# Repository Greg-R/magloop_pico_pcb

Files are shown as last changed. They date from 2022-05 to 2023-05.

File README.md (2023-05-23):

#  Printed Circuit Board for Magnetic Loop Antenna Controller

**Please note this repository is no longer active.**

The new repository is here:

(https://github.com/Greg-R/magloop_pico_pcb_2)

Design and fabrication files the Magnetic Loop Antenna Controller printed circuit board.

#  License

Please refer to the LICENSE file included in this repository.

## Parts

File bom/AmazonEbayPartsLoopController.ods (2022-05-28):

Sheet: Amazon
Amazon
Part | URL | Quantity for Project
Stepper Driver Module | https://www.amazon.com/gp/product/B01FFGAKK8
ILI9341 Display Module | https://www.amazon.com/gp/product/B073R7BH1B | 1
AD9850 DDS Module | https://www.amazon.com/gp/product/B01J7XPWNU | 1
Coaxial connector for relay | https://www.amazon.com/gp/product/B08Y7YWF3S | 1
Panel mount fuse holder and fuses | https://www.amazon.com/gp/product/B07VT4VRW7 | 1
Rotary encoders (not modules) with knobs | https://www.amazon.com/gp/product/B07DM2YMT4 | 3
Pushbuttons | https://www.amazon.com/gp/product/B0752RMB7Q | 3
Toggle switch for on/off | https://www.amazon.com/gp/product/B0799NSBHY | 1
Heatsink cooler fin for LM7805 | https://www.amazon.com/gp/product/B07MHT5KNP | 1
8 pin IDC connector with ribbon cable for display | https://www.amazon.com/gp/product/B07FKLHWT7 | 1
6 pin IDC connector with ribbon cable for push buttons and encoders | https://www.amazon.com/gp/product/B075PLZK9X | 2
JST connectors | https://www.amazon.com/gp/product/B01MCZE2HM | 3
JST crimping tool | https://www.amazon.com/gp/product/B01N4L8QMW | 1
Chanzon 1N5711, recommended diode | https://www.amazon.com/gp/product/B079KJBVZV | 4
Ethernet to screw terminal board, used at antenna | https://www.amazon.com/gp/product/B06XZ3BMTL | 1
Cat7 Ethernet Cable Outdoor rated | https://www.amazon.com/Outdoor-Ethernet-SNANSHI-1000Mbit-Waterproof/dp/B06ZZ1SKD6?th=1 | 1
Nylon hardware kit for assembling enclosure | https://www.amazon.com/HVAZI-Metric-Phillips-Screws-Assortment/dp/B07DVD95YY?th=1
Adhesive feet for controller enclosure | https://www.amazon.com/Bumper-Stopper-Protector-Adhesive-Headboard/dp/B0811DSRQB | 4
25 foot BNC cable | https://www.amazon.com/gp/product/B00K4D19IU?th=1 | 1
Plexiglas 10x10 | https://www.amazon.com/gp/product/B089P1KZ44?th=1 | 1
Large pulley 5mm bore | https://www.amazon.com/gp/product/B09NNBQP9T | 1
Small pulley 5mm bore | https://www.amazon.com/gp/product/B07DMWJJ6X?th=1 | 1
Belt, 6mm width, 260mm length | https://www.amazon.com/gp/product/B07B5Y4MGZ | 1
Limit switches | https://www.amazon.com/gp/product/B08CDF3Q6T | 2
Nylon bolts for antenna M8 30mm supports | https://www.amazon.com/gp/product/B012TAVQJW
Nylon bolts for tuner support brackets M8 40mm | https://www.amazon.com/gp/product/B0936RBF53
Nylon bolts for enclosure | https://www.amazon.com/gp/product/B07DVD95YY
Nylon bolts 6mm used on tuner assembly | https://www.amazon.com/gp/product/B07QWM86GX
DIP switches | https://www.amazon.com/gp/product/B07MH572VS | 1

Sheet: eBay
eBay
Part | URL | Quantity for Project
Substitute for cancelled Digikey BNC | https://www.ebay.com/itm/232652734283

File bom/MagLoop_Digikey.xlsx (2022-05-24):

Country of Origin may be different at time of shipment.
The HTSUS and ECCN information shown is for informational purposes only and is not a representation or warranty as to the accuracy or reliability of these classifications. All information is provided "as is" and is subject to change without notice. Any use made of the information provided is without recourse to Digi-Key and at the user's risk.
Index | Manufacturer Part Number | Manufacturer Name | Description | Availability | Stock Status | Attrition % | Requested Quantity 1 | Pack Quantity 1 | Pack Type 1 | Digi-Key Part Number 1 | Unit Price 1 | Extended Price 1 | Minimum Order Quantity 1 | Customer Reference | Requested Part Number | Lead Weeks | Datasheet | Reference Designator | US Import Tariff | Note | Part Status | RoHS Status | ECCN | HTSUS | Country of Origin | Environmental Information | Original Part numbers | Image
1 | PJ-036AH-SMT-TR | CUI Devices | CONN PWR JACK 2X5.5MM SOLDER | 63,562 | In Stock |  | 1 | 1 | Cut Tape (CT) | CP-036AHPJCT-ND | 1.43000 | $1.43 | 1 |  | CP-036AHPJCT-ND | 14 | https://www.cuidevices.com/product/resource/digikeypdf/pj-036ah-smt-tr.pdf |  | N/A |  | Active | ROHS3 Compliant | EAR99 | 8536.69.4040 | China | https://www.cuidevices.com/product/resource/material-compliance/pj-036ah-smt-tr | CP-036AHPJCT-ND | //media.digikey.com/photos/CUI%20Photos/MFG_PJ-036AH-SMT.jpg
2 | UVR1V100MDD | Nichicon | CAP ALUM 10UF 20% 35V RADIAL | 0 | Normally Stocking |  | 1 | 1 | Bulk | 493-1077-ND | 0.25000 | $0.25 | 1 |  | 493-1077-ND | 64 | https://download.datasheets.com/pdfs/2016/10/6/6/6/44/578/nch_/manual/93896153625063e-uvr.pdf |  | N/A |  | Active | ROHS3 Compliant | EAR99 | 8532.22.0020 | Malaysia |  | 493-1077-ND | //media.digikey.com/photos/Nichicon%20Photos/VR%20SERIES%20YELLOW%20HIGHLIGHT%20990-992.jpg
3 | ERJ-P08J752V | Panasonic Electronic Components | RES SMD 7.5K OHM 5% 2/3W 1206 | 2,311 | In Stock |  | 1 | 1 | Cut Tape (CT) | P7.5KALCT-ND | 0.17000 | $0.17 | 1 |  | P7.5KALCT-ND | 54 | https://industrial.panasonic.com/cdbs/www-data/pdf/RDO0000/AOA0000C331.pdf |  | N/A |  | Active | ROHS3 Compliant | EAR99 | 8533.21.0030 | Japan | https://industrial.panasonic.com/cdbs/www-cgi/auto-publishing.cgi?type=ROSU&region=WW&layer=4&cd=AOA0002 | P7.5KALCT-ND | //media.digikey.com/Renders/Panasonic%20Renders/ERJ-1206%20Pkg.jpg
4 | PPPC081LFBN-RC | Sullins Connector Solutions | CONN HDR 8POS 0.1 GOLD PCB | 92,192 | In Stock |  | 1 | 1 | Tray | S7041-ND | 0.67000 | $0.67 | 1 |  | S7041-ND | 11 | //media.digikey.com/pdf/Data%20Sheets/Sullins%20PDFs/Female_Headers.100_DS.pdf |  | N/A |  | Active | ROHS3 Compliant | EAR99 | 8536.69.4040 | Taiwan | https://www.sullinscorp.com/wp-content/uploads/2019/03/Sullins-RoHS-Compliant-Statement.pdf|https://www.sullinscorp.com/wp-content/uploads/2021/05/Sullins-REACH-211-SVHC-Compliant-Statement.pdf | S7041-ND | //media.digikey.com/photos/Sullins%20Photos/PPPC081LFBN-RC.jpg
5 | PPPC101LFBN-RC | Sullins Connector Solutions | CONN HDR 10POS 0.1 GOLD PCB | 130,868 | In Stock |  | 1 | 1 | Tray | S7043-ND | 0.68000 | $0.68 | 1 |  | S7043-ND | 11 | //media.digikey.com/pdf/Data%20Sheets/Sullins%20PDFs/Female_Headers.100_DS.pdf |  | N/A |  | Active | ROHS3 Compliant | EAR99 | 8536.69.4040 | Taiwan | https://www.sullinscorp.com/wp-content/uploads/2019/03/Sullins-RoHS-Compliant-Statement.pdf|https://www.sullinscorp.com/wp-content/uploads/2021/05/Sullins-REACH-211-SVHC-Compliant-Statement.pdf | S7043-ND | //media.digikey.com/photos/Sullins%20Photos/PPPC101LFBN-RC.jpg
6 | 2-406541-3 | TE Connectivity AMP Connectors | CONN MOD JACK 8P8C R/A SHIELDED | 6,301 | In Stock |  | 1 | 1 | Tray | A118429-ND | 2.57000 | $2.57 | 1 |  | A118429-ND | 27 | https://www.te.com/commerce/DocumentDelivery/DDEController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 |  | May apply on shipments to the U.S. |  | Active | RoHS Compliant | EAR99 | 8536.69.4040 | China |  | A118429-ND | //media.digikey.com/photos/TE%20Connectivity/2-406541-3.JPG
7 | ERJ-8GEYJ750V | Panasonic Electronic Components | RES SMD 75 OHM 5% 1/4W 1206 |  |  |  | 1 | 1 | Cut Tape (CT) | P75ECT-ND | 0.15000 | $0.15 | 1 |  | P75ECT-ND | 54 | https://industrial.panasonic.com/ww/products/pt/general-purpose-chip-resistors/models/ERJ8GEYJ750V |  | N/A |  |  | ROHS3 Compliant | EAR99 | 8533.21.0030 | Japan | https://industrial.panasonic.com/cdbs/www-cgi/auto-publishing.cgi?type=ROSU&region=WW&layer=4&cd=AOA0002 | P75ECT-ND | //media.digikey.com/Renders/Panasonic%20Renders/ERJ-1206%20Pkg.jpg
8 | RC1206FR-0710KL | YAGEO | RES 10K OHM 1% 1/4W 1206 | 2,137,700 | In Stock |  | 1 | 1 | Cut Tape (CT) | 311-10.0KFRCT-ND | 0.10000 | $0.10 | 1 |  | 311-10.0KFRCT-ND | 20 | https://www.yageo.com/upload/media/product/productsearch/datasheet/rchip/PYu-RC_Group_51_RoHS_L_11.pdf |  | May apply on shipments to the U.S. |  | Active | ROHS3 Compliant | EAR99 | 8533.21.0030 | Taiwan | https://www.yageo.com/en/Download/Index/certificates#rchip | 311-10.0KFRCT-ND | //media.digikey.com/Renders/Yageo%20Renders/Yageo-0603.jpg
9 | ERJ-8GEYJ513V | Panasonic Electronic Components | RES SMD 51K OHM 5% 1/4W 1206 |  |  |  | 1 | 1 | Cut Tape (CT) | P51KECT-ND | 0.15000 | $0.15 | 1 |  | P51KECT-ND | 54 | https://industrial.panasonic.com/ww/products/pt/general-purpose-chip-resistors/models/ERJ8GEYJ513V |  | N/A |  |  | ROHS3 Compliant | EAR99 | 8533.21.0030 | Japan | https://industrial.panasonic.com/cdbs/www-cgi/auto-publishing.cgi?type=ROSU&region=WW&layer=4&cd=AOA0002 | P51KECT-ND | //media.digikey.com/Renders/Panasonic%20Renders/ERJ-1206%20Pkg.jpg
10 | RMCF1206FT1K00 | Stackpole Electronics Inc | RES 1K OHM 1% 1/4W 1206 | 820,264 | In Stock |  | 1 | 1 | Cut Tape (CT) | RMCF1206FT1K00CT-ND | 0.10000 | $0.10 | 1 |  | RMCF1206FT1K00CT-ND | 17 | https://www.seielect.com/catalog/sei-rmcf_rmcp.pdf |  | May apply on shipments to the U.S. |  | Active | ROHS3 Compliant | EAR99 | 8533.21.0030 | Taiwan | https://www.seielect.com/catalog/reach.pdf|https://www.seielect.com/catalog/cert-of-compliance.pdf|https://www.seielect.com/catalog/SEI-RoHS_Compliance_Status.pdf | RMCF1206FT1K00CT-ND | //media.digikey.com/Renders/Stackpole%20Renders/1206.jpg
11 | PP3-002AH | CUI Devices | CONN PWR PLUG 2.1X5.5MM SOLDER | 3,286 | In Stock |  | 1 | 1 | Bag | CP3-002AH-ND | 1.64000 | $1.64 | 1 |  | CP3-002AH-ND | 15 | https://www.cuidevices.com/product/resource/digikeypdf/pp3-002ah.pdf |  | N/A |  | Active | ROHS3 Compliant | EAR99 | 8536.69.8000 | Taiwan | https://www.cuidevices.com/product/resource/material-compliance/pp3-002ah | CP3-002AH-ND | //media.digikey.com/Photos/CUI%20Photos/PP3-002AH.JPG
12 | 5-1634513-1 | TE Connectivity AMP Connectors | CONN BNC JACK R/A 50 OHM PCB |  | Obsolete |  | 1 |  |  |  |  |  |  |  | A97569-ND | 4 | https://www.te.com/commerce/DocumentDelivery/DDEController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 |  | N/A |  | Obsolete | RoHS Compliant | EAR99 | 8536.69.4010 | Taiwan | http://www.te.com/commerce/alt/SinglePartSearch.do?PN=5-1634513-1&dest=stmt | A97569-ND | //media.digikey.com/Photos/TE%20Connectivity/5-1634513-1.JPG
13 | S2G | SMC Diode Solutions | DIODE GEN PURP 400V 2A SMB | 21,388 | In Stock |  | 1 | 1 | Cut Tape (CT) | 1655-S2GCT-ND | 0.37000 | $0.37 | 1 |  | 1655-S2GCT-ND | 16 | https://www.smc-diodes.com/propdf/S2A-S2M%20N0562%20REV.A.pdf |  | May apply on shipments to the U.S. |  | Active | ROHS3 Compliant | EAR99 | 8541.10.0080 | China | http://www.smc-diodes.com/uploadfile/Declaration%20Letter%20for%20EU%20REACH-3.pdf|http://www.smc-diodes.com/uploadfile/ROHS%20Declaration%20Letter-3.pdf | 1655-S2GCT-ND | //media.digikey.com/Renders/SMC%20Diode%20Solutions/1655;SMB_DO214AA;;2.jpg
14 | CL31B104KBCNNNC | Samsung Electro-Mechanics | CAP CER 0.1UF 50V X7R 1206 | 1,739,651 | In Stock |  | 1 | 1 | Cut Tape (CT) | 1276-1017-1-ND | 0.12000 | $0.12 | 1 |  | 1276-1017-1-ND | 28 | //media.digikey.com/pdf/Data%20Sheets/Samsung%20PDFs/CL31B104KBCNNNC_Spec.pdf |  | N/A |  | Active | ROHS3 Compliant | EAR99 | 8532.24.0020 | Philippines | https://www.samsungsem.com/global/support/certificate/product-stewardship.do|https://www.samsungsem.com/files/fileDown.do?key=ed1dfdfa-645e-4252-b707-17f9b1502dd1 | 1276-1017-1-ND | //media.digikey.com/Renders/Samsung%20Electro-Mechanics%20America/Ceramic-Capacitor-CL-Series.jpg
15 | LM4040C30FTA | Diodes Incorporated | IC VREF SHUNT 0.5% SOT23 | 0 | Normally Stocking |  | 1 | 1 | Cut Tape (CT) | LM4040C30FTADICT-ND | 0.61000 | $0.61 | 1 |  | LM4040C30FTADICT-ND | 69 | https://www.diodes.com/assets/Datasheets/LM4040.pdf |  | May apply on shipments to the U.S. |  | Active | ROHS3 Compliant | EAR99 | 8542.39.0001 | China | https://www.diodes.com/assets/Quality-Reliability-Docs/Master_CofC.pdf | LM4040C30FTADICT-ND | //media.digikey.com/Renders/Diodes%20Renders/SOT-23-3%20PKG.jpg
16 | MBR0580-TP | Micro Commercial Co | DIODE SCHOTTKY 80V 500MA SOD123 | 108,267 | In Stock |  | 1 | 1 | Cut Tape (CT) | MBR0580-TPMSCT-ND | 0.35000 | $0.35 | 1 |  | MBR0580-TPMSCT-ND | 28 | https://www.mccsemi.com/pdf/Products/MBR0520-MBR0580(SOD123).pdf |  | May apply on shipments to the U.S. |  | Active | ROHS3 Compliant | EAR99 | 8541.10.0070 | China | https://www.mccsemi.com/pdf/pbfree/Certification%20of%20RoHS%20Compliance.pdf|https://www.mccsemi.com/pdf/pbfree/Certification%20of%20Compliance%20of%20CaliforniaProposition65.pdf|https://www.mccsemi.com/pdf/pbfree/Certification%20of%20REACH%20Compliance.pdf | MBR0580-TPMSCT-ND | //media.digikey.com/Renders/Micro%20Commercial%20Renders/SOD-123.jpg
17 | ERJ-8GEYJ472V | Panasonic Electronic Components | RES SMD 4.7K OHM 5% 1/4W 1206 | 144,268 | In Stock |  | 1 | 1 | Cut Tape (CT) | P4.7KECT-ND | 0.15000 | $0.15 | 1 |  | P4.7KECT-ND | 54 | https://industrial.panasonic.com/ww/products/pt/general-purpose-chip-resistors/models/ERJ8GEYJ472V |  | N/A |  |  | ROHS3 Compliant | EAR99 | 8533.21.0030 | Japan | https://industrial.panasonic.com/cdbs/www-cgi/auto-publishing.cgi?type=ROSU&region=WW&layer=4&cd=AOA0002 | P4.7KECT-ND | //media.digikey.com/Renders/Panasonic%20Renders/ERJ-1206%20Pkg.jpg
18 | CC1206KRX7R9BB471 | YAGEO | CAP CER 470PF 50V X7R 1206 | 39,533 | In Stock |  | 1 | 1 | Cut Tape (CT) | 311-1167-1-ND | 0.23000 | $0.23 | 1 |  | 311-1167-1-ND | 20 | https://www.yageo.com/upload/media/product/productsearch/datasheet/mlcc/UPY-GPHC_X7R_6.3V-to-50V_20.pdf |  | N/A |  | Active | ROHS3 Compliant | EAR99 | 8532.24.0020 | Taiwan |  | 311-1167-1-ND | //media.digikey.com/Renders/Yageo%20Renders/1206%280%5E7mm%20thickness%29.jpg
19 | B2B-XH-A-GU | JST Sales America Inc. | CONN HEADER VERT 2POS 2.5MM | 54,025 | In Stock |  | 1 | 1 | Bulk | 455-2946-ND | 0.24000 | $0.24 | 1 |  | 455-2946-ND | 34 | https://www.jst-mfg.com/product/pdf/eng/eXH.pdf |  | N/A |  | Active | RoHS Compliant | EAR99 | 8536.69.4040 | China |  | 455-2946-ND | //media.digikey.com/Photos/JST%20Photos/B2B-XH-A-GU.JPG
20 | DMP31D0U-7 | Diodes Incorporated | MOSFET P-CH 30V 530MA SOT23 | 649 | In Stock |  | 1 | 1 | Cut Tape (CT) | DMP31D0U-7DICT-ND | 0.47000 | $0.47 | 1 |  | DMP31D0U-7DICT-ND | 90 | https://www.diodes.com/assets/Datasheets/DMP31D0U.pdf |  | May apply on shipments to the U.S. |  | Active | ROHS3 Compliant | EAR99 | 8541.21.0095 | China | https://www.diodes.com/assets/Quality-Reliability-Docs/Master_CofC.pdf | DMP31D0U-7DICT-ND | //media.digikey.com/Renders/Diodes%20Renders/SOT-23-3%20PKG.jpg
21 | MMBT3904,215 | Nexperia USA Inc. | TRANS NPN 40V 0.2A TO236AB | 507,080 | In Stock |  | 1 | 1 | Cut Tape (CT) | 1727-4044-1-ND | 0.12000 | $0.12 | 1 |  | 1727-4044-1-ND | 27 | https://assets.nexperia.com/documents/data-sheet/MMBT3904.pdf |  | May apply on shipments to the U.S. |  | Active | ROHS3 Compliant | EAR99 | 8541.21.0075 | China |  | 1727-4044-1-ND | //media.digikey.com/Photos/Nexperia/MFG_SOT23.jpg
22 | LM358P | Texas Instruments | IC OPAMP GP 2 CIRCUIT 8DIP | 13,317 | In Stock |  | 2 | 2 | Tube | 296-1395-5-ND | 0.49000 | $0.98 | 1 |  | 296-1395-5-ND | 35 | https://www.ti.com/general/docs/suppproductinfo.tsp?distId=10 |  | May apply on shipments to the U.S. |  | Active | ROHS3 Compliant | EAR99 | 8542.33.0001 | China |  | 296-1395-5-ND | //media.digikey.com/Photos/Rochester/MFG_TC254P.jpg.jpg
23 | ERJ-8GEYJ272V | Panasonic Electronic Components | RES SMD 2.7K OHM 5% 1/4W 1206 | 149,367 | In Stock |  | 1 | 1 | Cut Tape (CT) | P2.7KECT-ND | 0.15000 | $0.15 | 1 |  | P2.7KECT-ND | 54 | https://industrial.panasonic.com/ww/products/pt/general-purpose-chip-resistors/models/ERJ8GEYJ272V |  | N/A |  |  | ROHS3 Compliant | EAR99 | 8533.21.0030 | Japan | https://industrial.panasonic.com/cdbs/www-cgi/auto-publishing.cgi?type=ROSU&region=WW&layer=4&cd=AOA0002 | P2.7KECT-ND | //media.digikey.com/Renders/Panasonic%20Renders/ERJ-1206%20Pkg.jpg
24 | ERJ-8ENF5100V | Panasonic Electronic Components | RES SMD 510 OHM 1% 1/4W 1206 | 76,423 | In Stock |  | 1 | 1 | Cut Tape (CT) | P510FCT-ND | 0.20000 | $0.20 | 1 |  | P510FCT-ND | 54 | https://industrial.panasonic.com/cdbs/www-data/pdf/RDA0000/AOA0000C304.pdf |  | N/A |  |  | ROHS3 Compliant | EAR99 | 8533.21.0030 | Japan | https://industrial.panasonic.com/cdbs/www-cgi/auto-publishing.cgi?type=ROSU&region=WW&layer=4&cd=AOA0002 | P510FCT-ND | //media.digikey.com/Renders/Panasonic%20Renders/ERJ-1206%20Pkg.jpg
25 | ERJ-P08J201V | Panasonic Electronic Components | RES SMD 200 OHM 5% 2/3W 1206 | 15,554 | In Stock |  | 1 | 1 | Cut Tape (CT) | P200ALCT-ND | 0.17000 | $0.17 | 1 |  | P200ALCT-ND | 54 | https://industrial.panasonic.com/cdbs/www-data/pdf/RDO0000/AOA0000C331.pdf |  | N/A |  | Active | ROHS3 Compliant | EAR99 | 8533.21.0030 | Japan | https://industrial.panasonic.com/cdbs/www-cgi/auto-publishing.cgi?type=ROSU&region=WW&layer=4&cd=AOA0002 | P200ALCT-ND | //media.digikey.com/Renders/Panasonic%20Renders/ERJ-1206%20Pkg.jpg
26 | ERJ-8ENF43R0V | Panasonic Electronic Components | RES SMD 43 OHM 1% 1/4W 1206 | 56,385 | In Stock |  | 1 | 1 | Cut Tape (CT) | P43.0FCT-ND | 0.20000 | $0.20 | 1 |  | P43.0FCT-ND | 54 | https://industrial.panasonic.com/cdbs/www-data/pdf/RDA0000/AOA0000C304.pdf |  | N/A |  |  | ROHS3 Compliant | EAR99 | 8533.21.0030 | Japan | https://industrial.panasonic.com/cdbs/www-cgi/auto-publishing.cgi?type=ROSU&region=WW&layer=4&cd=AOA0002 | P43.0FCT-ND | //media.digikey.com/Renders/Panasonic%20Renders/ERJ-1206%20Pkg.jpg
27 | ERJ-8GEYJ391V | Panasonic Electronic Components | RES SMD 390 OHM 5% 1/4W 1206 | 211,714 | In Stock |  | 1 | 1 | Cut Tape (CT) | P390ECT-ND | 0.15000 | $0.15 | 1 |  | P390ECT-ND | 54 | https://industrial.panasonic.com/ww/products/pt/general-purpose-chip-resistors/models/ERJ8GEYJ391V |  | N/A |  |  | ROHS3 Compliant | EAR99 | 8533.21.0030 | Japan | https://industrial.panasonic.com/cdbs/www-cgi/auto-publishing.cgi?type=ROSU&region=WW&layer=4&cd=AOA0002 | P390ECT-ND | //media.digikey.com/Renders/Panasonic%20Renders/ERJ-1206%20Pkg.jpg
28 | ERJ-8ENF24R9V | Panasonic Electronic Components | RES SMD 24.9 OHM 1% 1/4W 1206 | 5,357 | In Stock |  | 1 | 1 | Cut Tape (CT) | P24.9FCT-ND | 0.20000 | $0.20 | 1 |  | P24.9FCT-ND | 54 | https://industrial.panasonic.com/cdbs/www-data/pdf/RDA0000/AOA0000C304.pdf |  | N/A |  |  | ROHS3 Compliant | EAR99 | 8533.21.0030 | Japan | https://industrial.panasonic.com/cdbs/www-cgi/auto-publishing.cgi?type=ROSU&region=WW&layer=4&cd=AOA0002 | P24.9FCT-ND | //media.digikey.com/Renders/Panasonic%20Renders/ERJ-1206%20Pkg.jpg
29 | ERJ-8GEYJ222V | Panasonic Electronic Components | RES SMD 2.2K OHM 5% 1/4W 1206 | 1,505,502 | In Stock |  | 1 | 1 | Cut Tape (CT) | P2.2KECT-ND | 0.15000 | $0.15 | 1 |  | P2.2KECT-ND | 54 | https://industrial.panasonic.com/ww/products/pt/general-purpose-chip-resistors/models/ERJ8GEYJ222V |  | N/A |  |  | ROHS3 Compliant | EAR99 | 8533.21.0030 | Japan | https://industrial.panasonic.com/cdbs/www-cgi/auto-publishing.cgi?type=ROSU&region=WW&layer=4&cd=AOA0002 | P2.2KECT-ND | //media.digikey.com/Renders/Panasonic%20Renders/ERJ-1206%20Pkg.jpg
30 | ERJ-8GEYJ510V | Panasonic Electronic Components | RES SMD 51 OHM 5% 1/4W 1206 | 43,802 | In Stock |  | 1 | 1 | Cut Tape (CT) | P51ECT-ND | 0.15000 | $0.15 | 1 |  | P51ECT-ND | 54 | https://industrial.panasonic.com/ww/products/pt/general-purpose-chip-resistors/models/ERJ8GEYJ510V |  | N/A |  |  | ROHS3 Compliant | EAR99 | 8533.21.0030 | Japan | https://industrial.panasonic.com/cdbs/www-cgi/auto-publishing.cgi?type=ROSU&region=WW&layer=4&cd=AOA0002 | P51ECT-ND | //media.digikey.com/Renders/Panasonic%20Renders/ERJ-1206%20Pkg.jpg
31 | ERJ-8GEYJ105V | Panasonic Electronic Components | RES SMD 1M OHM 5% 1/4W 1206 | 116,279 | In Stock |  | 1 | 1 | Cut Tape (CT) | P1.0MECT-ND | 0.15000 | $0.15 | 1 |  | P1.0MECT-ND | 54 | https://industrial.panasonic.com/ww/products/pt/general-purpose-chip-resistors/models/ERJ8GEYJ105V |  | N/A |  |  | ROHS3 Compliant | EAR99 | 8533.21.0030 | Japan | https://industrial.panasonic.com/cdbs/www-cgi/auto-publishing.cgi?type=ROSU&region=WW&layer=4&cd=AOA0002 | P1.0MECT-ND | //media.digikey.com/Renders/Panasonic%20Renders/ERJ-1206%20Pkg.jpg
32 | ERJ-8GEYJ243V | Panasonic Electronic Components | RES SMD 24K OHM 5% 1/4W 1206 | 20,248 | In Stock |  | 1 | 1 | Cut Tape (CT) | P24KECT-ND | 0.15000 | $0.15 | 1 |  | P24KECT-ND | 54 | https://industrial.panasonic.com/ww/products/pt/general-purpose-chip-resistors/models/ERJ8GEYJ243V |  | N/A |  |  | ROHS3 Compliant | EAR99 | 8533.21.0030 | Japan | https://industrial.panasonic.com/cdbs/www-cgi/auto-publishing.cgi?type=ROSU&region=WW&layer=4&cd=AOA0002 | P24KECT-ND | //media.digikey.com/Renders/Panasonic%20Renders/ERJ-1206%20Pkg.jpg
33 | PPPC201LFBN-RC | Sullins Connector Solutions | CONN HDR 20POS 0.1 GOLD PCB | 14,630 | In Stock |  | 1 | 1 | Tray | S7053-ND | 1.28000 | $1.28 | 1 |  | S7053-ND | 11 | //media.digikey.com/pdf/Data%20Sheets/Sullins%20PDFs/Female_Headers.100_DS.pdf |  | N/A |  | Active | ROHS3 Compliant | EAR99 | 8536.69.4040 | Taiwan | https://www.sullinscorp.com/wp-content/uploads/2019/03/Sullins-RoHS-Compliant-Statement.pdf|https://www.sullinscorp.com/wp-content/uploads/2021/05/Sullins-REACH-211-SVHC-Compliant-Statement.pdf | S7053-ND | //media.digikey.com/photos/Sullins%20Photos/PPPC201LFBN-RC.jpg
34 | PH1-20-UA | Adam Tech | CONN HEADER VERT 20POS 2.54MM | 11,761 | In Stock |  | 1 | 1 | Bag | 2057-PH1-20-UA-ND | 0.32000 | $0.32 | 1 |  | 2057-PH1-20-UA-ND | 10 | https://app.adam-tech.com/products/download/data_sheet/201605/ph1-xx-ua-data-sheet.pdf |  | N/A |  | Active | ROHS3 Compliant | EAR99 | 8536.69.4040 | Taiwan |  | 2057-PH1-20-UA-ND | //media.digikey.com/Renders/Adam-Tech%20Renders/PH1-xx-UA.jpg

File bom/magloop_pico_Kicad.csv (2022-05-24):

Source: | /home/raven/gitrepos/pcb/magloop_pico_pcb/magloop_pico.kicad_sch
Date: | Tue 24 May 2022 03:14:49 PM EDT
Tool: | Eeschema 6.0.5-a6ca702e91~116~ubuntu20.04.1
Generator: | /usr/share/kicad/plugins/bom_csv_grouped_by_value_with_fp.py
Component Count: | 102
Ref | Qnty | Value | Cmp name | Footprint | Description | Vendor
C1, C6, C7, C19, | 4 | 10 uF | C_Polarized_US | Capacitor_THT:CP_Radial_D5.0mm_P2.00mm | Polarized capacitor, US symbol
C2, C3, C4, C5, C8, C9, C10, C13, C14, C15, C16, C17, C18, C20, C23, C24, C25, C28, C29, | 19 | 0.1uF | C | Capacitor_SMD:C_1206_3216Metric_Pad1.33x1.80mm_HandSolder | Unpolarized capacitor
C11, C12, C21, C22, C26, C27, | 6 | 470pF | C | Capacitor_SMD:C_1206_3216Metric_Pad1.33x1.80mm_HandSolder | Unpolarized capacitor
D1, | 1 | MBR0520LT1G | MBR0520LT1G | digikey-footprints:SOD-123 | DIODE SCHOTTKY 20V 500MA SOD123
D2, D3, D4, D5, | 4 | 1N5711 | 1N5711UR | Diode_THT:D_DO-35_SOD27_P7.62mm_Horizontal | 70V 33mA Schottky diode, MELF(DO-213AA)
D6, | 1 | 1N4004 | 1N4004 | Diode_SMD:D_SMB | 400V 1A General Purpose Rectifier Diode, DO-41
FB1, | 1 | FerriteBead | FerriteBead | Inductor_SMD:L_1206_3216Metric | Ferrite bead
J1, | 1 | Conn_Coaxial_Power | Conn_Coaxial_Power | Connector_BarrelJack:BarrelJack_CUI_PJ-036AH-SMT_Horizontal | coaxial connector (BNC, SMA, SMB, SMC, Cinch/RCA, LEMO, ...)
J2, J4, | 2 | Conn_02x03_Odd_Even | Conn_02x03_Odd_Even | Connector_IDC:IDC-Header_2x03_P2.54mm_Vertical | Generic connector, double row, 02x03, odd/even pin numbering scheme (row 1 odd numbers, row 2 even numbers), script generated (kicad-library-utils/schlib/autogen/connector/)
J3, | 1 | POWER SW | B2B-XH-A_LF__SN_ | digikey-footprints:PinHeader_1x2_P2.5mm_Drill1.1mm | CONN HEADER VERT 2POS 2.5MM
J5, | 1 | Conn_02x04_Odd_Even | Conn_02x04_Odd_Even | Connector_IDC:IDC-Header_2x04_P2.54mm_Vertical | Generic connector, double row, 02x04, odd/even pin numbering scheme (row 1 odd numbers, row 2 even numbers), script generated (kicad-library-utils/schlib/autogen/connector/)
J6, | 1 | TO RF RELAY | B2B-XH-A_LF__SN_ | digikey-footprints:PinHeader_1x2_P2.5mm_Drill1.1mm | CONN HEADER VERT 2POS 2.5MM
J7, | 1 | ETHERNET | 2-406541-3 | magloop_library:2-406541-3
J8, | 1 | 5-1634513-1 | 5-1634513-1 | 5-1634513-1:TE_5-1634513-1
J9, | 1 | 12V AUDIO MUTE | B2B-XH-A_LF__SN_ | digikey-footprints:PinHeader_1x2_P2.5mm_Drill1.1mm | CONN HEADER VERT 2POS 2.5MM
J10, | 1 | 5V AUDIO MUTE | B2B-XH-A_LF__SN_ | digikey-footprints:PinHeader_1x2_P2.5mm_Drill1.1mm | CONN HEADER VERT 2POS 2.5MM
Q1, Q2, Q3, Q4, Q5, Q6, Q7, Q9, Q11, | 9 | NPN | MMBT3904 | Package_TO_SOT_SMD:SOT-23_Handsoldering | 0.2A Ic, 40V Vce, Small Signal NPN Transistor, SOT-23
Q8, Q10, Q12, | 3 | PMOS | Si2371EDS | Package_TO_SOT_SMD:SOT-23_Handsoldering | -3.6A Id, -30V Vds, P-Channel MOSFET, SOT-23
R1, | 1 | 7.5K | R_US | Resistor_SMD:R_1206_3216Metric_Pad1.30x1.75mm_HandSolder | Resistor, US symbol
R2, | 1 | 2.7K | R_US | Resistor_SMD:R_1206_3216Metric_Pad1.30x1.75mm_HandSolder | Resistor, US symbol
R3, | 1 | 510 | R_US | Resistor_SMD:R_1206_3216Metric_Pad1.30x1.75mm_HandSolder | Resistor, US symbol
R4, | 1 | 200 | R_US | Resistor_SMD:R_1206_3216Metric_Pad1.30x1.75mm_HandSolder | Resistor, US symbol
R5, | 1 | 43 | R_US | Resistor_SMD:R_1206_3216Metric_Pad1.30x1.75mm_HandSolder | Resistor, US symbol
R6, | 1 | 75 | R_US | Resistor_SMD:R_1206_3216Metric_Pad1.30x1.75mm_HandSolder | Resistor, US symbol
R7, | 1 | 390 | R_US | Resistor_SMD:R_1206_3216Metric_Pad1.30x1.75mm_HandSolder | Resistor, US symbol
R8, | 1 | 2.2K | R_US | Resistor_SMD:R_1206_3216Metric_Pad1.30x1.75mm_HandSolder | Resistor, US symbol
R10, | 1 | 24.9 | R_US | Resistor_SMD:R_1206_3216Metric_Pad1.30x1.75mm_HandSolder | Resistor, US symbol
R13, R14, R15, R16, | 4 | 51.0 | R_US | Resistor_SMD:R_1206_3216Metric_Pad1.30x1.75mm_HandSolder | Resistor, US symbol
R17, R18, | 2 | 4.7K | R_US | Resistor_SMD:R_1206_3216Metric_Pad1.30x1.75mm_HandSolder | Resistor, US symbol
R20, R21, | 2 | 1M | R_US | Resistor_SMD:R_1206_3216Metric_Pad1.30x1.75mm_HandSolder | Resistor, US symbol
R22, R23, | 2 | 51K | R_US | Resistor_SMD:R_1206_3216Metric_Pad1.30x1.75mm_HandSolder | Resistor, US symbol
R24, R25, | 2 | 1K | R_US | Resistor_SMD:R_1206_3216Metric_Pad1.30x1.75mm_HandSolder | Resistor, US symbol
R26, R27, R30, R31, R32, R33, R34, R35, R36, R37, R38, R39, R40, | 13 | 10K | R_US | Resistor_SMD:R_1206_3216Metric_Pad1.30x1.75mm_HandSolder | Resistor, US symbol
R28, R29, | 2 | 24K | R_US | Resistor_SMD:R_1206_3216Metric_Pad1.30x1.75mm_HandSolder | Resistor, US symbol
SW1, | 1 | SW_DIP_x03 | SW_DIP_x03 | digikey-footprints:DIP-6_W7.62mm | 3x DIP Switch, Single Pole Single Throw (SPST) switch, small symbol
U1, | 1 | AD9850MODULE | AD9850MODULE | magloop_pico:AD9850_MODULE
U2, | 1 | A4988_Module | A4988_Module | magloop_pico:A4988_MODULE
U3, | 1 | LM7805 | LM7805_TO220 | Package_TO_SOT_THT:TO-220-3_Vertical | Positive 1A 35V Linear Regulator, Fixed Output 5V, TO-220
U4, | 1 | PI_PICO | PI_PICO | magloop_pico:PI_PICO
U5, | 1 | LM4040DBZ-3 | LM4040DBZ-3 | Package_TO_SOT_SMD:SOT-23_Handsoldering | 3.000V Precision Micropower Shunt Voltage Reference, SOT-23
U7, U8, | 2 | LM358 | LM358 | Package_DIP:DIP-8_W7.62mm | Low-Power, Dual Operational Amplifiers, DIP-8/SOIC-8/TO-99-8

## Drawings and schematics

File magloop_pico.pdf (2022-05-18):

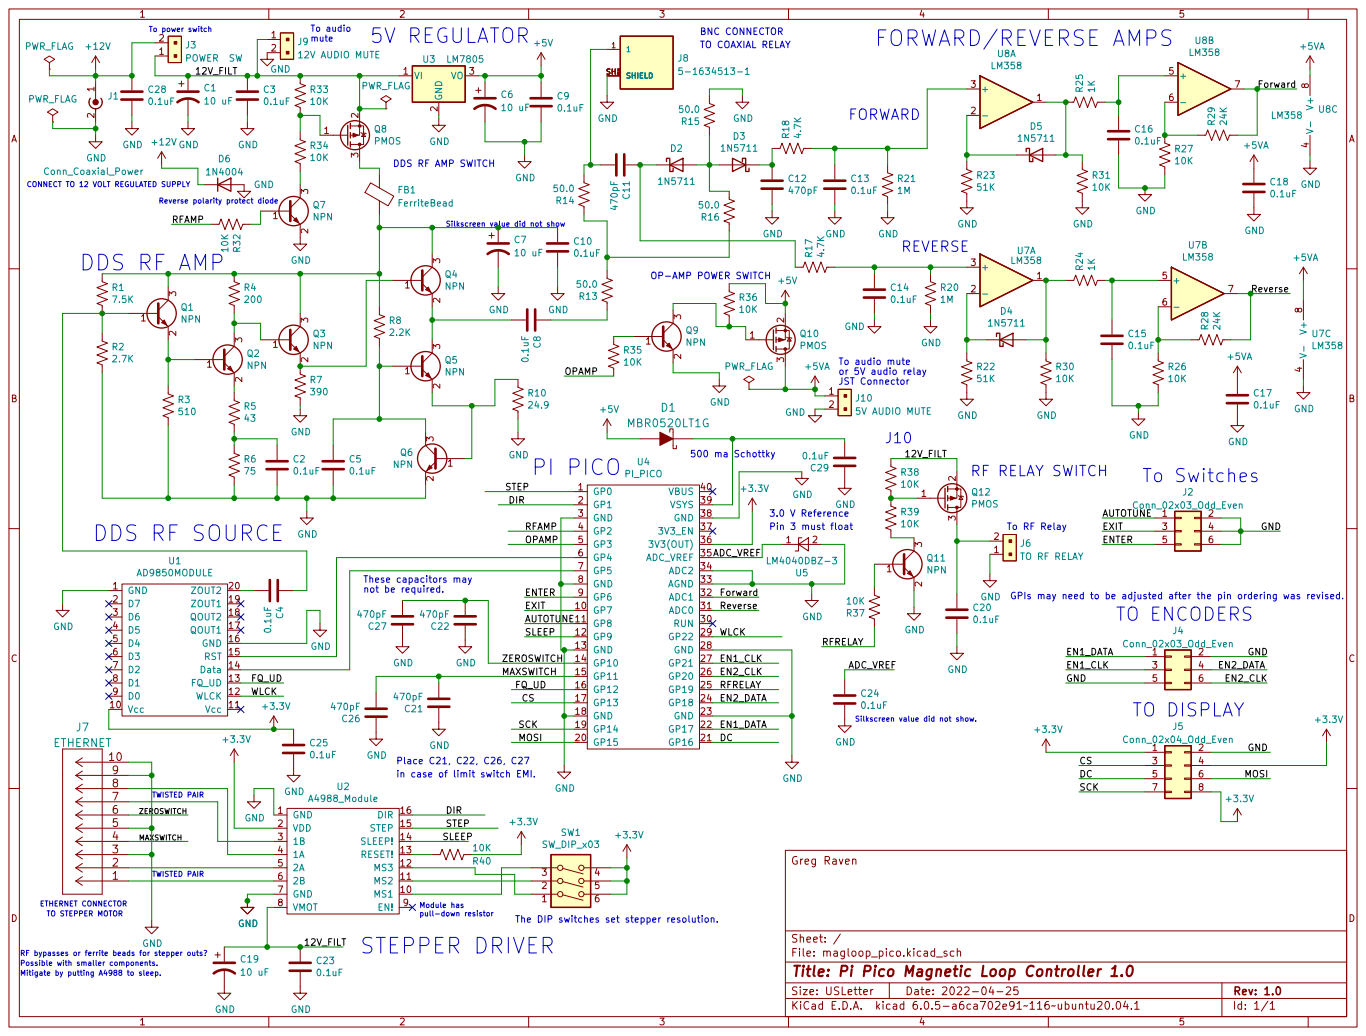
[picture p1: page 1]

To power switch CONNECT TO 12 VOLT REGULATED SUPPLY
PWR_FLAG

GPIs may need to be adjusted after the pin ordering was revised. DDS RF AMP SWITCH

Silkscreen value did not show

2 3 Q12 PMOS GND GND GND

3.0 V Reference Pin 3 must float DDS RF AMP

OP-AMP POWER SWITCH

not be required. TO STEPPER MOTOR

Silkscreen value did not show. TWISTED PAIR

7 | TWISTED PAIR

File: magloop_pico.kicad_sch Sheet: / Greg Raven

The DIP switches set stepper resolution.

RF bypasses or ferrite beads for stepper outs? Possible with smaller components.

Id: 1/1 Title: Pi Pico Magnetic Loop Controller 1.0

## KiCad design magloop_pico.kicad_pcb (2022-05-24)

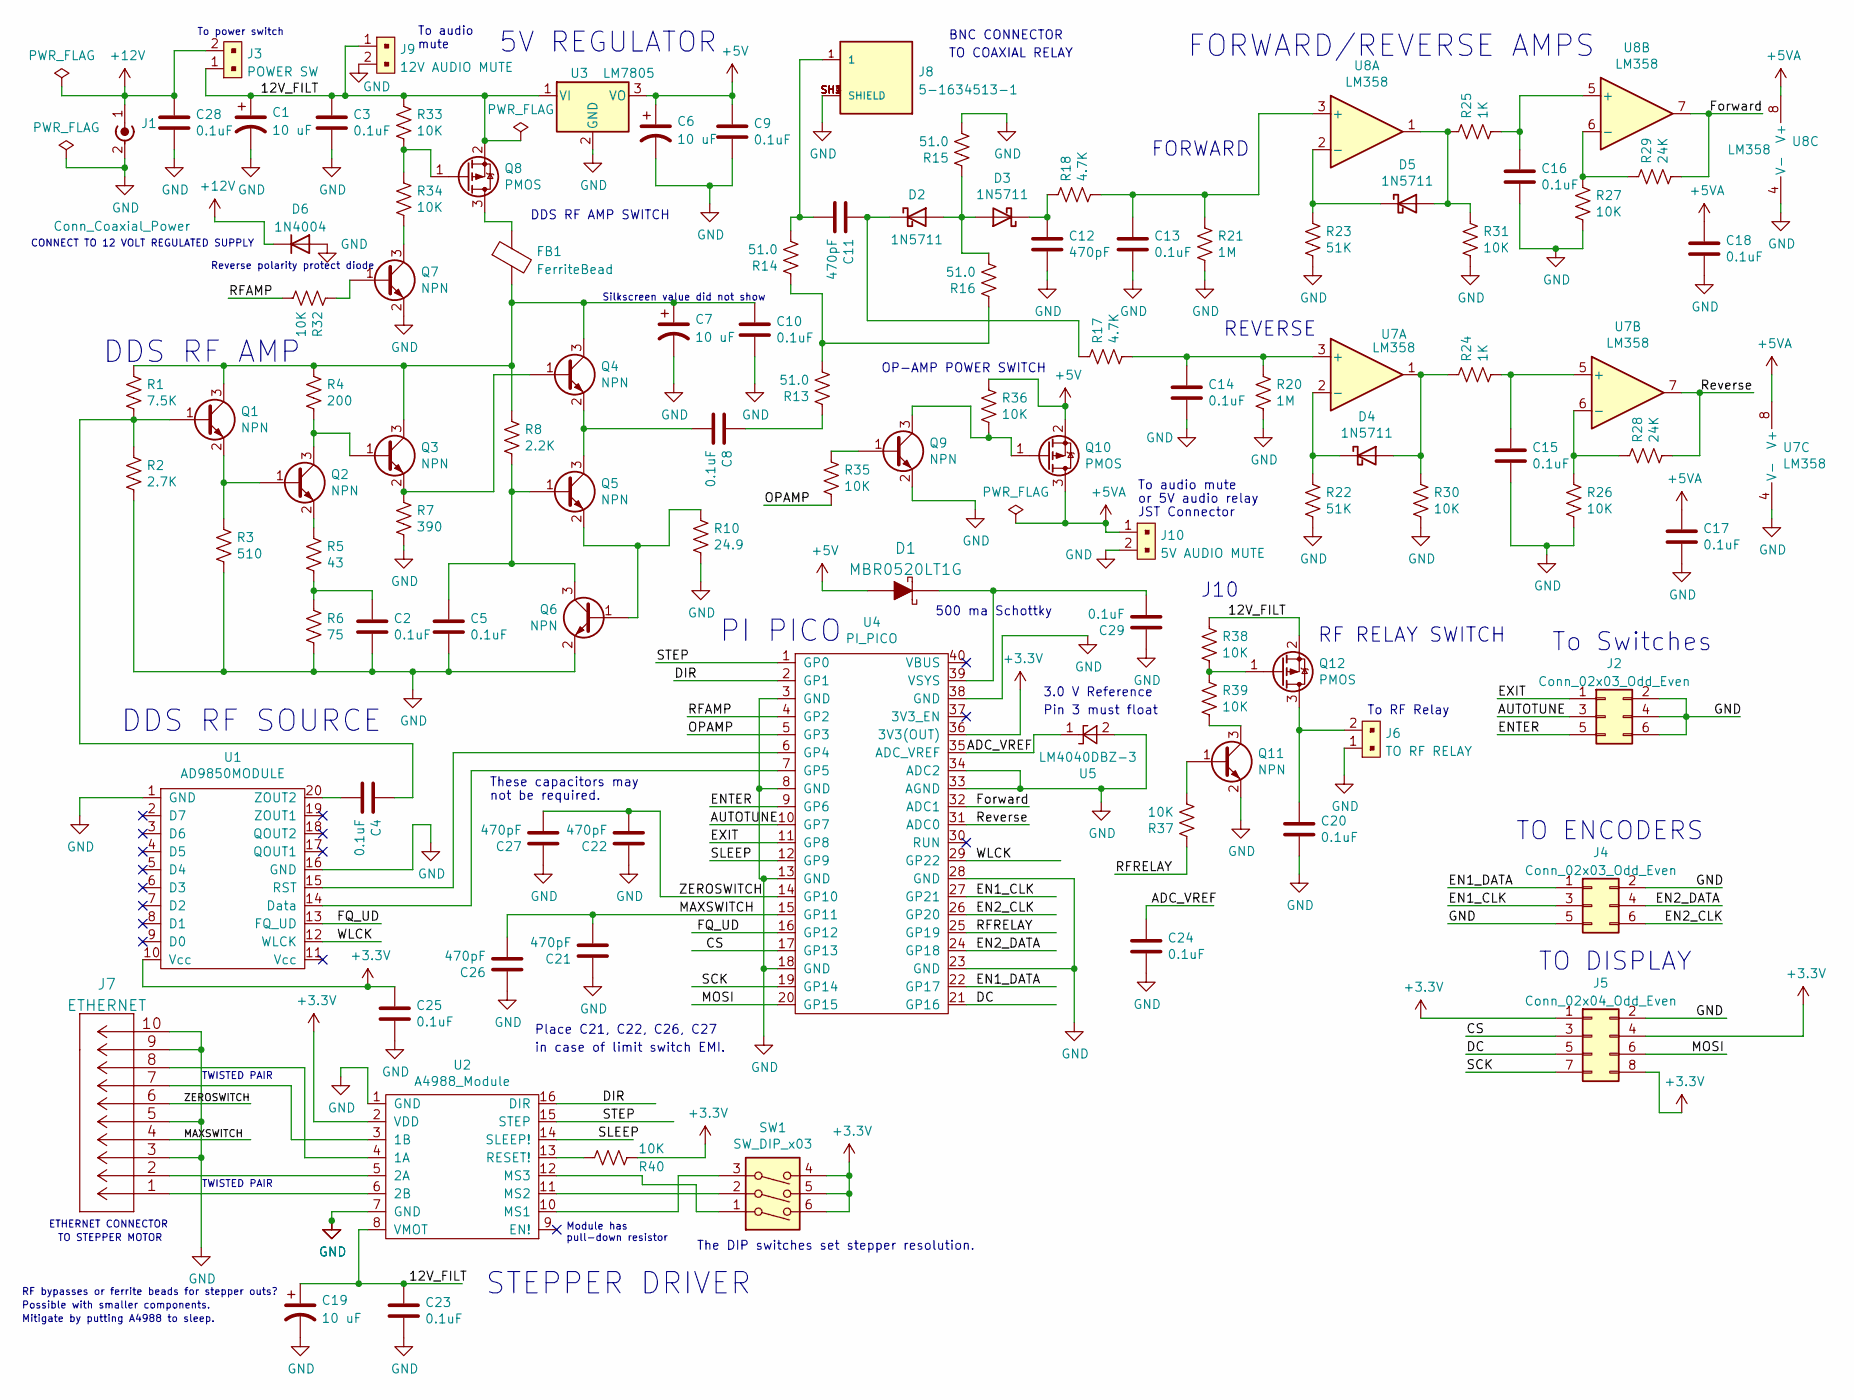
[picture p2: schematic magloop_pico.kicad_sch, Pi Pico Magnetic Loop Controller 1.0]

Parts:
C1, C6, C7, C19: 10 uF; CP_Radial_D5.0mm_P2.00mm
C2, C3, C4, C5, C8, C9, C10, C13, C14, C15, C16, C17, C18, C20, C23, C24, C25, C28, C29: 0.1uF; C_1206_3216Metric_Pad1.33x1.80mm_HandSolder
C11, C12, C21, C22, C26, C27: 470pF; C_1206_3216Metric_Pad1.33x1.80mm_HandSolder
D1: MBR0520LT1G; SOD-123; MPN MBR0520LT1G; Digi-Key_PN MBR0520LT1GOSCT-ND
D2, D3, D4, D5: 1N5711; D_DO-35_SOD27_P7.62mm_Horizontal
D6: 1N4004; D_SMB
FB1: FerriteBead; L_1206_3216Metric
J1: Conn_Coaxial_Power; BarrelJack_CUI_PJ-036AH-SMT_Horizontal
J2, J4: Conn_02x03_Odd_Even; IDC-Header_2x03_P2.54mm_Vertical
J3: POWER SW; PinHeader_1x2_P2.5mm_Drill1.1mm; MPN B2B-XH-A(LF)(SN); Digi-Key_PN 455-2247-ND
J5: Conn_02x04_Odd_Even; IDC-Header_2x04_P2.54mm_Vertical
J6: TO RF RELAY; PinHeader_1x2_P2.5mm_Drill1.1mm; MPN B2B-XH-A(LF)(SN); Digi-Key_PN 455-2247-ND
J7: ETHERNET; 2-406541-3
J8: 5-1634513-1; TE_5-1634513-1
J9: 12V AUDIO MUTE; PinHeader_1x2_P2.5mm_Drill1.1mm; MPN B2B-XH-A(LF)(SN); Digi-Key_PN 455-2247-ND
J10: 5V AUDIO MUTE; PinHeader_1x2_P2.5mm_Drill1.1mm; MPN B2B-XH-A(LF)(SN); Digi-Key_PN 455-2247-ND
Q1, Q2, Q3, Q4, Q5, Q6, Q7, Q9, Q11: NPN; SOT-23_Handsoldering
Q8, Q10, Q12: PMOS; SOT-23_Handsoldering
R1: 7.5K; R_1206_3216Metric_Pad1.30x1.75mm_HandSolder
R2: 2.7K; R_1206_3216Metric_Pad1.30x1.75mm_HandSolder
R3: 510; R_1206_3216Metric_Pad1.30x1.75mm_HandSolder
R4: 200; R_1206_3216Metric_Pad1.30x1.75mm_HandSolder
R5: 43; R_1206_3216Metric_Pad1.30x1.75mm_HandSolder
R6: 75; R_1206_3216Metric_Pad1.30x1.75mm_HandSolder
R7: 390; R_1206_3216Metric_Pad1.30x1.75mm_HandSolder
R8: 2.2K; R_1206_3216Metric_Pad1.30x1.75mm_HandSolder
R10: 24.9; R_1206_3216Metric_Pad1.30x1.75mm_HandSolder
R13, R14, R15, R16: 51.0; R_1206_3216Metric_Pad1.30x1.75mm_HandSolder
R17, R18: 4.7K; R_1206_3216Metric_Pad1.30x1.75mm_HandSolder
R20, R21: 1M; R_1206_3216Metric_Pad1.30x1.75mm_HandSolder
R22, R23: 51K; R_1206_3216Metric_Pad1.30x1.75mm_HandSolder
R24, R25: 1K; R_1206_3216Metric_Pad1.30x1.75mm_HandSolder
R26, R27, R30, R31, R32, R33, R34, R35, R36, R37, R38, R39, R40: 10K; R_1206_3216Metric_Pad1.30x1.75mm_HandSolder
R28, R29: 24K; R_1206_3216Metric_Pad1.30x1.75mm_HandSolder
SW1: SW_DIP_x03; DIP-6_W7.62mm
U1: AD9850MODULE; AD9850_MODULE
U2: A4988_Module; A4988_MODULE
U3: LM7805; TO-220-3_Vertical
U4: PI_PICO
U5: LM4040DBZ-3; SOT-23_Handsoldering
U7, U8: LM358; DIP-8_W7.62mm

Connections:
+3V3: C25.1, J5.1, J5.4, J5.8, R40.1, SW1.4, SW1.5, SW1.6, U1.10 (Vcc), U2.2 (VDD), U4.36 (3V3(OUT))
+5V: C6.1, C9.1, D1.A, Q10.2 (S), R36.1, U3.3 (VO)
+5VA: C17.1, C18.1, J10.1, Q10.3 (D), U7.8 (V+), U8.8 (V+)
+12V: C28.1, D6.1 (K), J1.1 (In), J3.2
/12V_FILT: C1.1, C3.1, C19.1, C23.1, J3.1, J9.1, Q8.2 (S), Q12.2 (S), R33.1, R38.1, U2.8 (VMOT), U3.1 (VI)
/ADC_VREF: C24.1, U4.35 (ADC_VREF), U5.1 (K)
/AUTOTUNE: J2.3, U4.10 (GP7)
/CS: J5.3, U4.17 (GP13)
/DC: J5.5, U4.21 (GP16)
/DIR: U2.16 (DIR), U4.2 (GP1)
/EN1_CLK: J4.3, U4.27 (GP21)
/EN1_DATA: J4.1, U4.22 (GP17)
/EN2_CLK: J4.6, U4.26 (GP20)
/EN2_DATA: J4.4, U4.24 (GP18)
/ENTER: J2.5, U4.9 (GP6)
/EXIT: J2.1, U4.11 (GP8)
/FQ_UD: U1.13 (FQ_UD), U4.16 (GP12)
/Forward: R29.2, U4.32 (ADC1), U8.7
/MAXSWITCH: C21.2, C26.2, J7.4, U4.15 (GP11)
/MOSI: J5.6, U4.20 (GP15)
/OPAMP: R35.2, U4.5 (GP3)
/RFAMP: R32.2, U4.4 (GP2)
/RFRELAY: R37.1, U4.25 (GP19)
/Reverse: R28.2, U4.31 (ADC0), U7.7
/SCK: J5.7, U4.19 (GP14)
/SLEEP: U2.14 (SLEEP!), U4.12 (GP9)
/STEP: U2.15 (STEP), U4.1 (GP0)
/WLCK: U1.12 (WLCK), U4.29 (GP22)
/ZEROSWITCH: C22.2, C27.2, J7.6, U4.14 (GP10)
GND: C1.2, C2.2, C3.2, C5.2, C6.2, C7.2, C9.2, C10.2, C12.2, C13.2, C14.2, C15.2, C16.2, C17.2, C18.2, C19.2, C20.2, C21.1, C22.1, C23.2, C24.2, C25.2, C26.1, C27.1, C28.2, C29.1, D6.2 (A), J1.2 (Ext), J2.2, J2.4, J2.6, J4.2, J4.5, J5.2, J6.1, J7.3, J7.5, J7.9, J7.10, J8.SH1 (SHIELD), J8.SH2 (SHIELD), J8.SH3 (SHIELD), J8.SH4 (SHIELD), J9.2, J10.2, Q6.2 (E), Q7.2 (E), Q9.2 (E), Q11.2 (E), R2.2, R3.2, R6.2, R7.2, R10.2, R15.2, R20.2, R21.2, R22.2, R23.2, R26.2, R27.2, R30.2, R31.2, U1.1 (GND), U1.16 (GND), U2.1 (GND), U2.7 (GND), U3.2 (GND), U4.3 (GND), U4.8 (GND), U4.13 (GND), U4.18 (GND), U4.23 (GND), U4.28 (GND), U4.33 (AGND), U4.34 (ADC2), U4.38 (GND), U5.2 (A), U7.4 (V-), U8.4 (V-)
unnamed: C2.1, R5.2, R6.1
unnamed: C4.1, Q1.1 (B), R1.2, R2.1
unnamed: C4.2, U1.20 (ZOUT2)
unnamed: C5.1, Q5.1 (B), Q6.3 (C), R8.2
unnamed: C8.1, R13.1
unnamed: C8.2, Q4.2 (E), Q5.3 (C)
unnamed: C7.1, C10.1, FB1.2, Q1.3 (C), Q3.3 (C), Q4.3 (C), R1.1, R4.1, R8.1
unnamed: C11.1, D2.1 (K), R17.1
unnamed: C11.2, J8.1, R14.2
unnamed: C12.1, D3.1 (K), R18.1
unnamed: C13.1, R18.2, R21.1, U8.3 (+)
unnamed: C14.1, R17.2, R20.1, U7.3 (+)
unnamed: C15.1, R24.2, U7.5 (+)
unnamed: C16.1, R25.2, U8.5 (+)
unnamed: C20.1, J6.2, Q12.3 (D)
unnamed: C29.2, D1.K, U4.39 (VSYS)
unnamed: D2.2 (A), D3.2 (A), R15.1, R16.2
unnamed: D4.1 (K), R22.1, U7.2 (-)
unnamed: D4.2 (A), R24.1, R30.1, U7.1
unnamed: D5.1 (K), R23.1, U8.2 (-)
unnamed: D5.2 (A), R25.1, R31.1, U8.1
unnamed: FB1.1, Q8.3 (D)
unnamed: J7.1, U2.6 (2B)
unnamed: J7.2, U2.5 (2A)
unnamed: J7.7, U2.3 (1B)
unnamed: J7.8, U2.4 (1A)
unnamed: Q1.2 (E), Q2.1 (B), R3.1
unnamed: Q2.2 (E), R5.1
unnamed: Q2.3 (C), Q3.1 (B), R4.2
unnamed: Q3.2 (E), Q4.1 (B), R7.1
unnamed: Q5.2 (E), Q6.1 (B), R10.1
unnamed: Q7.1 (B), R32.1
unnamed: Q7.3 (C), R34.2
unnamed: Q8.1 (G), R33.2, R34.1
unnamed: Q9.1 (B), R35.1
unnamed: Q9.3 (C), Q10.1 (G), R36.2
unnamed: Q11.1 (B), R37.2
unnamed: Q11.3 (C), R39.2
unnamed: Q12.1 (G), R38.2, R39.1
unnamed: R13.2, R14.1, R16.1
unnamed: R26.1, R28.1, U7.6 (-)
unnamed: R27.1, R29.1, U8.6 (-)
unnamed: R40.2, U2.13 (RESET!)
unnamed: SW1.1, U2.12 (MS3)
unnamed: SW1.2, U2.11 (MS2)
unnamed: SW1.3, U2.10 (MS1)
unnamed: U1.14 (Data), U4.7 (GP5)
unnamed: U1.15 (RST), U4.6 (GP4)

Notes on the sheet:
To RF Relay
CONNECT TO 12 VOLT REGULATED SUPPLY
PI PICO
STEPPER DRIVER
To audio mute
JST Connector
The DIP switches set stepper resolution.
BNC CONNECTOR
To Switches
Reverse polarity protect diode
DDS RF AMP SWITCH
or 5V audio relay
TWISTED PAIR
ETHERNET CONNECTOR
Silkscreen value did not show
Module has pull-down resistor
TO STEPPER MOTOR
J10
RF bypasses or ferrite beads for stepper outs?
OP-AMP POWER SWITCH
5V REGULATOR
REVERSE
To audio
To power switch
DDS RF SOURCE
TO COAXIAL RELAY
Place C21, C22, C26, C27
TO ENCODERS
500 ma Schottky
FORWARD
DDS RF AMP
These capacitors may
Possible with smaller components.
TO DISPLAY
Mitigate by putting A4988 to sleep.
FORWARD/REVERSE AMPS
Pin 3 must float
3.0 V Reference
mute
not be required.

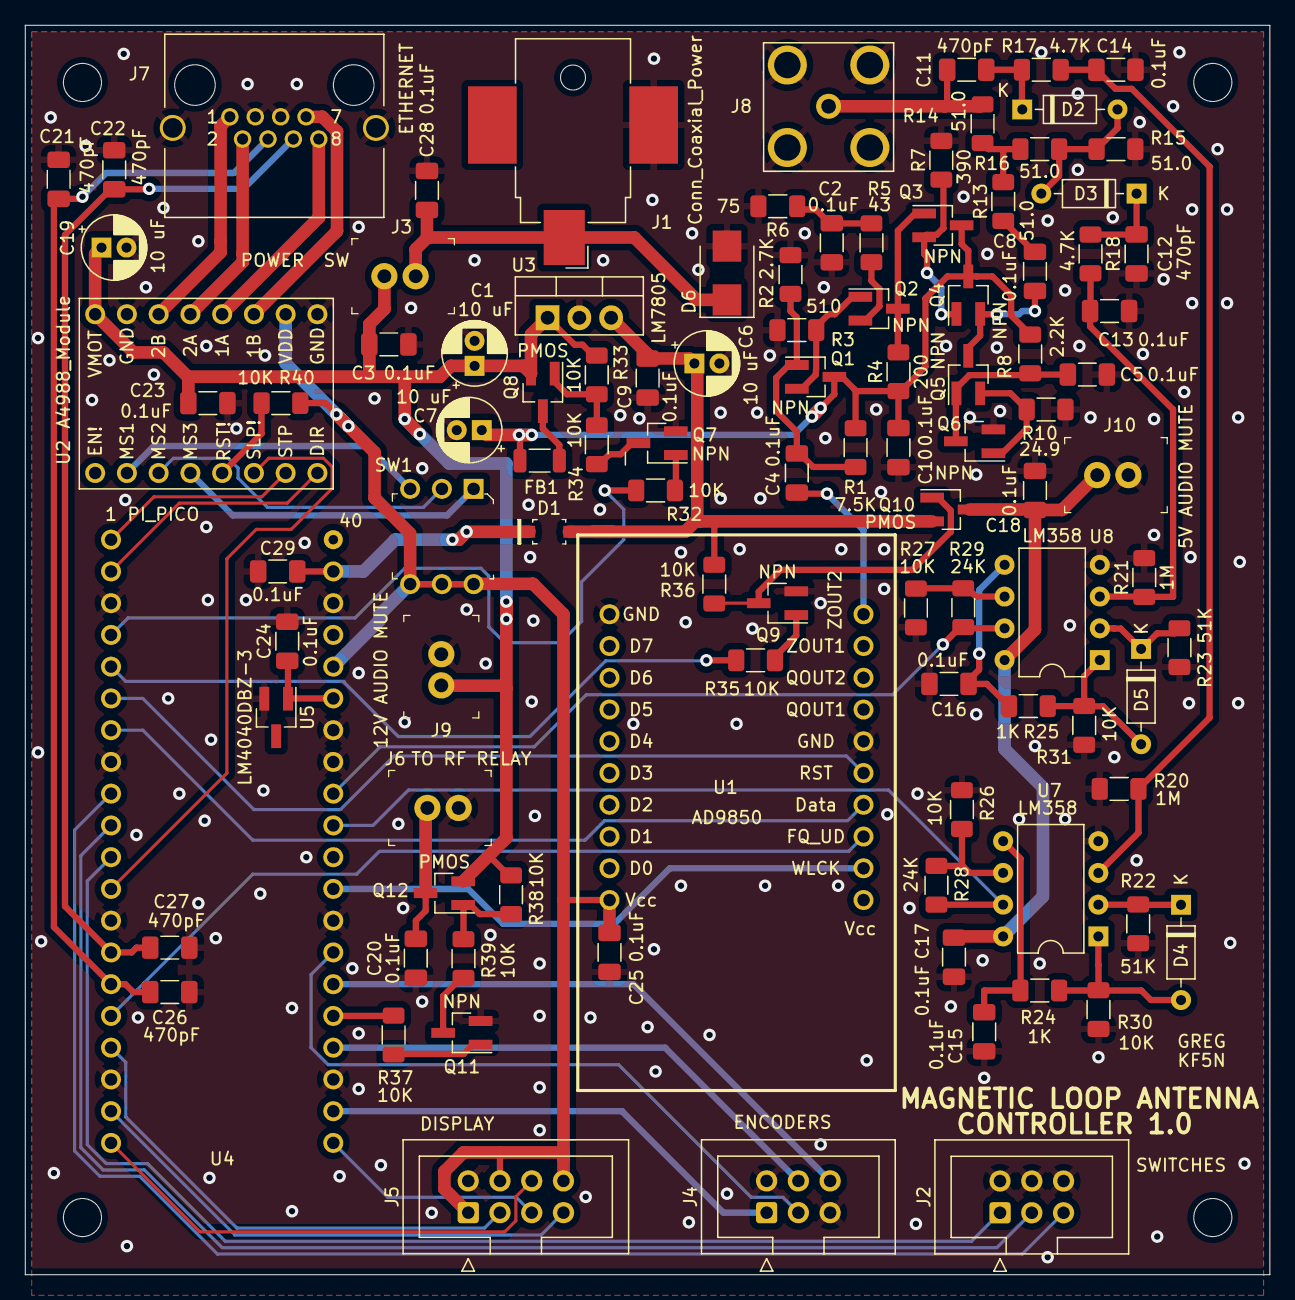
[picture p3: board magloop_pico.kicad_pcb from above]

Board: 2 copper layers, 99.6 x 99.9 mm, 102 parts (0 on the bottom side), 78 nets.

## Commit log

2022-05-09 Initial commit.
    [magloop_pico-B_Cu.gbl, magloop_pico-B_Mask.gbs, magloop_pico-B_Silkscreen.gbo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]
2022-05-15 Added BOM directory
    [AmazonPartsLoopController.ods, magloop_pico.kicad_sch]
2022-05-18 Added schematic PDF.
2022-05-24 Added BOMs from Digikey and Kicad schematic. Minor clean up top metal and changed 50 ohm resistors to 51.
    [AmazonPartsLoopController.ods, MagLoop_Digikey.xlsx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]
2022-05-28 Added alternative source for BNC connector (eBay).
    [AmazonEbayPartsLoopController.ods, AmazonPartsLoopController.ods]
2022-05-28 A Kicad file got changed.

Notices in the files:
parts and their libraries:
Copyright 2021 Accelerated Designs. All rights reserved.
